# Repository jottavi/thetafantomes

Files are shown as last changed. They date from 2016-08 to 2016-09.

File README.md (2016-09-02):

# Documentation Thêta Fantômes

---
## L'installation

### Mise en place

 1. Brancher le routeur wifi.
 2. Attendre que le voyant wifi soit allumé.
 3. Brancher les batteries sur les circuits jaune des plateformes (PAS SUR LA BLEUE, RISQUE DE DESTRUCTION).
 4. La plateforme devrait faire un bruit strident, elle est en marche.
 5. Brancher le module de contrôle des lasers.

### Troubleshooting

*"La plateforme fait un bruit étrange et ne roule pas correctement, voir vibre."*

* La batterie est probablement vide, il faut la recharger ou en utiliser une autre pleine.

*"La plateforme ne roule pas correctement, les moteurs ne forcent pas ou forcent peu lors de la mise sous tension et ne font pas de bruit, voir vibrent."*

* Les drivers n'envoient peut-être pas assez de courant aux moteurs. Il faut donc tourner chaque potentiomètre des drivers avec UN TOURNE VIS CÉRAMIQUE jusqu'à ce qu'ils fassent un bruit et que les moteurs soient bloqués.

*"Un moteur ne fonctionne pas du tout, n'est pas bloqué, et même en tournant le potentiomètre du driver cela n'a aucun effet."*

* Le driver est probablement grillé. Il faut tester avec un nouveau driver.

*"La plateforme est sous tension, fait du bruit mais n'avance pas lorsque l'ordinateur lui envoie une information."*

* Vous avez surement branché les plateformes trop tôt après avoir branché le routeur wifi, attendez que le voyant WIFI de celui-ci s'allume pour débranchez et rebranchez la plateforme.

*"Le module de contrôle des lasers est sous tension mais les lasers ne bougent pas lorsque l'ordinateur lui envoie une information."*

* Vous avez surement branché le module trop tôt après avoir branché le routeur wifi, attendez que le voyant WIFI de celui-ci s'allume pour débrancher et rebrancher le module de contrôle des lasers.

## Technique

À [cette adresse](https///github.com/jottavi/thetafantomes), vous trouverez le dossier contenant :

* le code
* les librairies
* les pièces 3D
* les circuits imprimés
* les drivers

### Wifi

#### Network

Voici les IP et les ports sur lesquels les dispositifs fonctionnent :

<table>
	<thead>
		<tr>
			<th>Dispositifs</th>
			<th>IP</th>
			<th>PORT</th>
			<th>Envoi / Réception</th>
		</tr>
	</thead>
	<tbody>
		<tr>
			<td>Master Machine</td>
			<td>192.168.168.100</td>
			<td>7110</td>
			<td>Envoi &gt; Broadcast</td>
		</tr>
		<tr>
			<td>Laptop Player 1</td>
			<td>192.168.168.101</td>
			<td>7110</td>
			<td>Envoi &gt; Broadcast</td>
		</tr>
		<tr>
			<td>Laptop Player 2</td>
			<td>192.168.168.102</td>
			<td>7110</td>
			<td>Envoi &gt; Broadcast</td>
		</tr>
		<tr>
			<td>Laptop Player 3</td>
			<td>192.168.168.103</td>
			<td>7110</td>
			<td>Envoi &gt; Broadcast</td>
		</tr>
		<tr>
			<td>Laptop Player 4</td>
			<td>192.168.168.104</td>
			<td>7110</td>
			<td>Envoi &gt; Broadcast</td>
		</tr>
		<tr>
			<td>Lasers</td>
			<td>192.168.168.200</td>
			<td>7110</td>
			<td>Réception &gt; 192.168.168.101-102-103-104</td>
		</tr>
		<tr>
			<td>Plateforme Player 1 (Alpha)</td>
			<td>192.168.168.201</td>
			<td>7110</td>
			<td>Réception &gt; 192.168.168.101</td>
		</tr>
		<tr>
			<td>Plateforme Player 2 (Bravo)</td>
			<td>192.168.168.202</td>
			<td>7110</td>
			<td>Réception &gt; 192.168.168.102</td>
		</tr>
		<tr>
			<td>Plateforme Player 3 (Charlie)</td>
			<td>192.168.168.203</td>
			<td>7110</td>
			<td>Réception &gt; 192.168.168.103</td>
		</tr>
		<tr>
			<td>Plateforme Player 4 (Tango)</td>
			<td>192.168.168.204</td>
			<td>7110</td>
			<td>Réception &gt; 192.168.168.104</td>
		</tr>
	</tbody>
</table>

Le module de contrôle des lasers écoute sur toutes les IPs des ordinateurs des joueurs et actionne le laser correspondant au joueur attribué.

Les messages OSC peuvent être envoyés jusqu'à 10 millisecondes sur les lasers, pas moins. Peut-être plus pour les plateformes.

Voici les messages OSC réceptionnés par les dispositifs (plateformes et lasers) :

<table>
	<thead>
		<tr>
			<th colspan="3">Plateformes</th>
		</tr>
		<tr>
			<th>Route</th>
			<th>Valeurs</th>
			<th>Effet</th>
		</tr>
	</thead>
	<tbody>
		<tr>
			<td>/speed</td>
			<td>-10000 => 10000</td>
			<td>Vitesse</td>
		</tr>
		<tr>
			<td>/angle</td>
			<td>-180 => 180</td>
			<td>Rotation</td>
		</tr>
	</tbody>
	</tr>
</table>

<table>
	<thead>
		<tr>
			<th colspan="3">Lasers</th>
		</tr>
		<tr>
			<th>Route</th>
			<th>Valeurs</th>
			<th>Effet</th>
		</tr>
	</thead>
	<tbody>
		<tr>
			<td>/x</td>
			<td>0 => 127</td>
			<td>Position X</td>
		</tr>
		<tr>
			<td>/y</td>
			<td>0 => 127</td>
			<td>Position Y</td>
		</tr>
		<tr>
			<td>/blink</td>
			<td>0 => 171 (0 = OFF / 171 = ON)</td>
			<td>Clignotement</td>
		</tr>
	</tbody>
	</tr>
</table>

#### Programmation

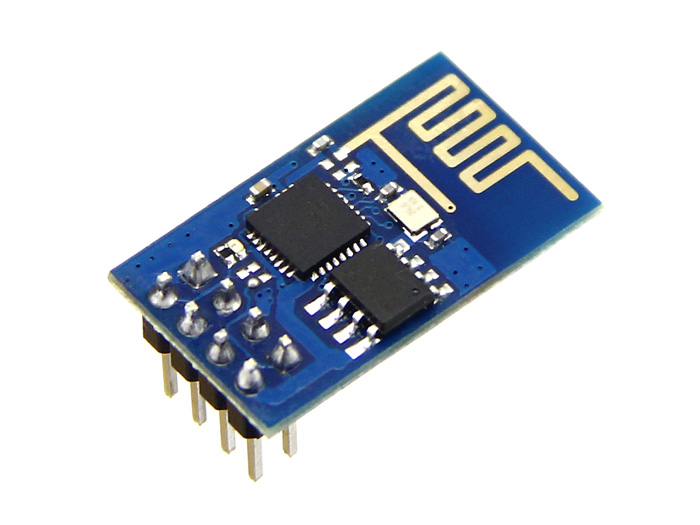
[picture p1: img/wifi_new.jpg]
ESP8266


Le module wifi utilisé (ESP8266) contient un petit microcontrôleur programmable et une puce wifi.  
Aussi, pour une meilleur gestion des messages OSC, le module a dû être reprogrammé à partir de l'IDE arduino, en y installant une librairie de gestion du protocole OSC.  
Vous trouverez la documentation de cette librairie à [cet endroit](https///github.com/CNMAT/OSC), et le reste des fonctions se trouvent [ici](http://cnmat.berkeley.edu/library/oscuino/).  
La version utilisée est adaptée pour l'ESP8266, vous la trouverez dans le dossier du projet et à [cette adresse](https///github.com/sandeepmistry/esp8266-OSC).  
Vous pouvez toujours remettre le firmware d'origine, disponible sur le site d'espressif.

Le module MOD-WIFI-ESP8266 de chez Olimex est un mauvais choix de version de module, nécessitant une soudure pour pouvoir le reprogrammer (voir image ci-dessous). En revanche, d'autres modules sont excellents, comme le NodeMcu Lua ESP8266, utilisable plus facilement en standalone, sans arduino, mais sur lequel il est difficile d'ajouter un shield.  

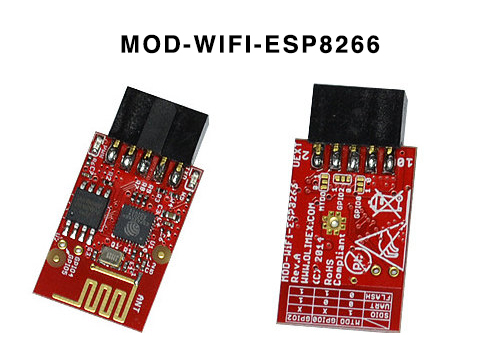
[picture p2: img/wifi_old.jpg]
MOD-WIFI-ESP8266


Il est nécessaire d'installer des outils pour pouvoir flasher ces modules avec un nouveau code.

##### Installation des outils de programmation dans l'IDE arduino

Pour commencer à programmer les ESP8266, vous aurez besoin d'installer les librairies relatives à ce module :

* Lancez arduino.
* Aller dans *Arduino > Préférences*.
* Sur cette fenêtre, entrez l'url *http://arduino.esp8266.com/stable/package\_esp8266com\_index.json* dans le champs *"URL de gestionnaire de cartes supplémentaires"* (Image ci-dessous).

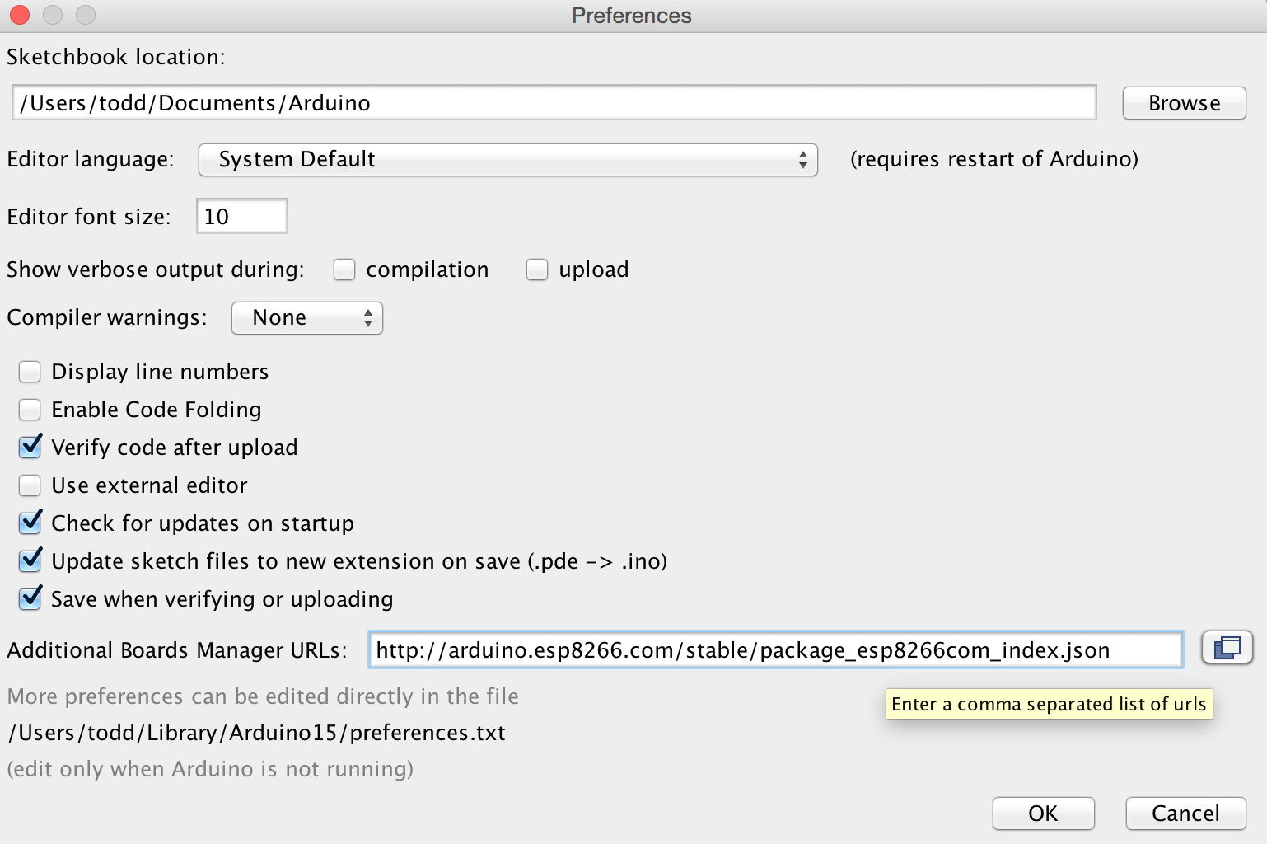
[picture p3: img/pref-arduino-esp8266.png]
Ajouter une URL de manager de cartes


* Cliquez sur OK.
* Allez dans *Outils > Type de carte > Gestionnaire de carte*.
* Dans cette fenêtre, recherchez *"esp8266"* et installez la librairie correspondante (voir ci-dessous).

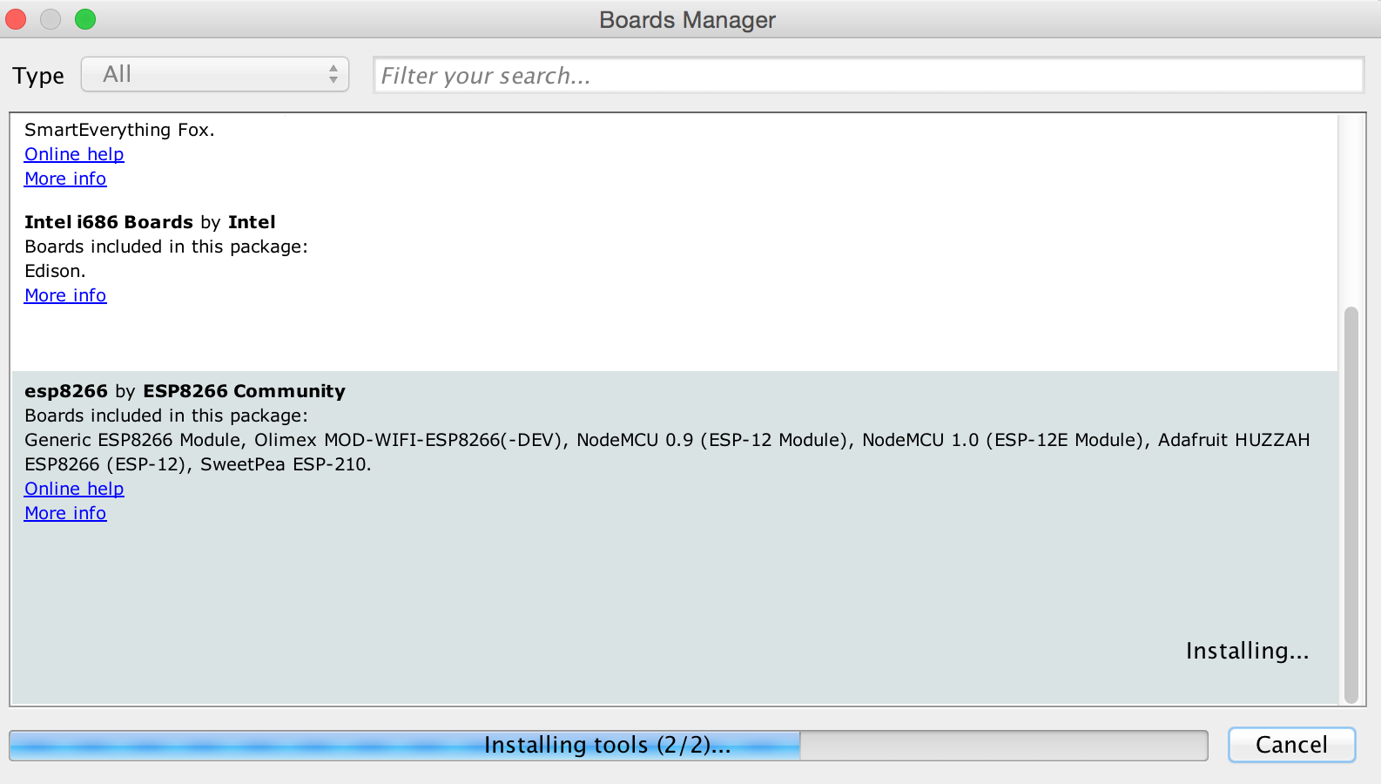
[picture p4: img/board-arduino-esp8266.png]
Installer le module ESP8266 sur l'IDE arduino


##### Installation du programmeur de l'ESP8266

Pour programmer ce module, nous allons avoir besoin de ce programmeur (voir image), plus simple à utiliser, basé sur la puce CH340.

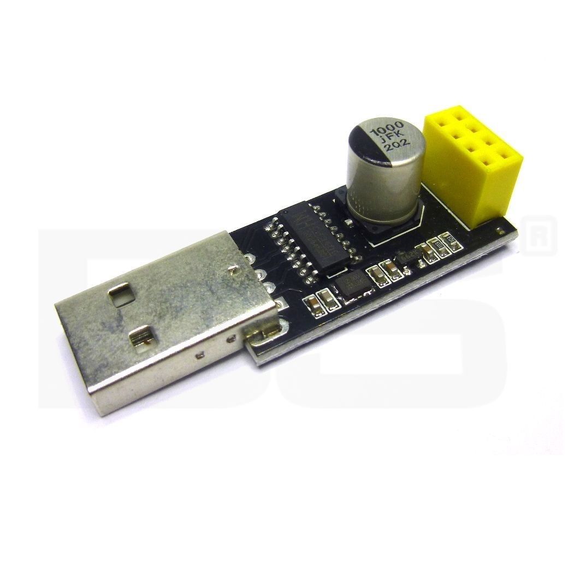
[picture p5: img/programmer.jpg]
Programmeur de l'ESP8266


Les drivers pour cette puce et les instructions d'installation sont présents à [cette page](http://sparks.gogo.co.nz/ch340.html).  
Vous les retrouverez dans le dossier du projet, disponible sur github. Sur linux, il n'est peut-être pas nécessaire de les installer.

##### Uploader un sketch sur l'ESP8266

Une fois ces étapes réalisées, vous devez sélectionner certains paramètres afin de programmer le module.

* Dans Arduino, allez dans *Outils > Type de Carte* et choisissez *"Generic ESP8266 Module"*.

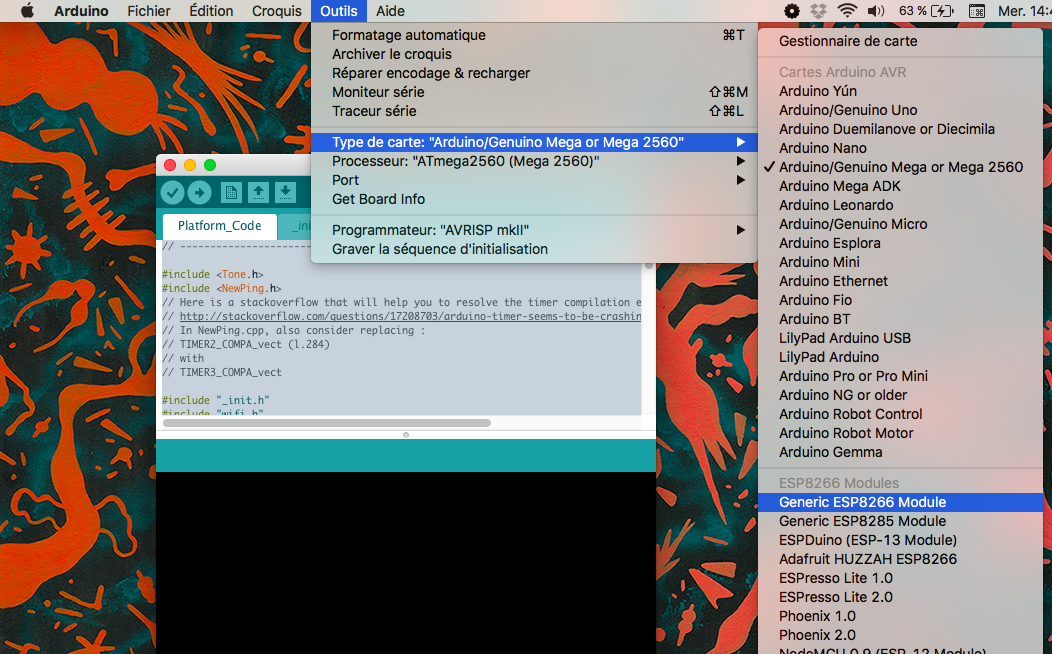
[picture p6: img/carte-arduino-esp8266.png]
Carte à selectionner


* Ensuite, lorsque le programmeur est branché, allez dans *Outils > Port* et choisissez *"/dev/cu.wchusbserial410"*.

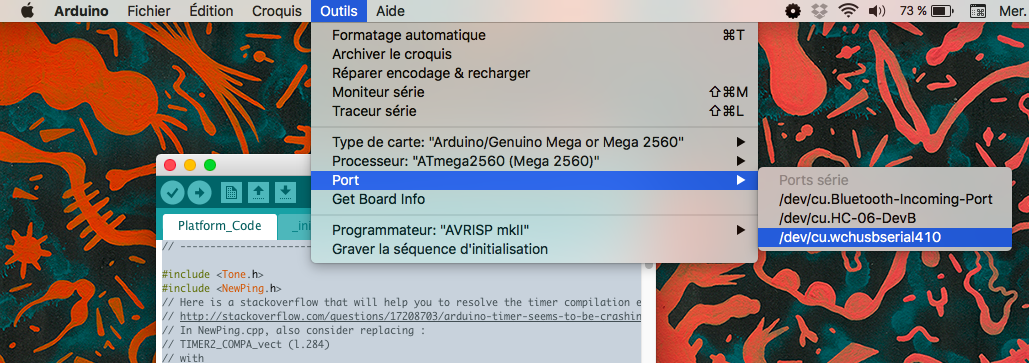
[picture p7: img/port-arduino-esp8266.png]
Port à selectionner


* Vous pouvez uploader le code.

### Lasers

Le code des lasers est très simple et met en oeuvre une Arduino Uno, un module wifi ESP8266 et un Tinkerkit Dmx Master Shield.  
Comme pour les plateformes, le module wifi relaie l'information osc vers l'arduino uno qui pilote les lasers via le shield DMX.

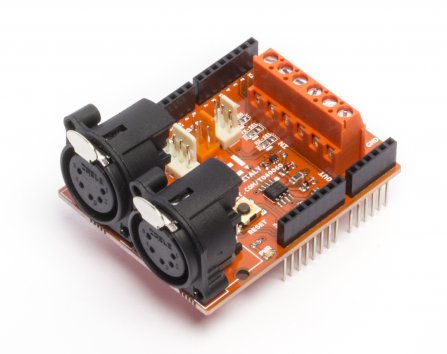
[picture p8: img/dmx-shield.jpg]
Tinkerkit DMX Master Shield


En revanche, le shield DMX comprend des embases XLR femelles 5 broches non compatibles avec les câbles XLR 3 broches couramment utilisés.  
Voici un schéma de montage pour construire un adaptateur XLR 5 broches vers XLR 3 broches afin de rendre ces câbles compatibles avec le shield.

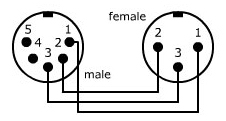
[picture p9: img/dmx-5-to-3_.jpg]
DMX 5 broches vers 3 broches


Le shield est pilotable par la librairie DmxSimple, disponible dans le dossier du projet et utilise la broche digital 3 de l'arduino UNO pour envoyer les commandes DMX.

Ces librairies se trouvent dans le dossier du projet. Vous trouverez la page de DmxSimple à [cette adresse](https///github.com/PaulStoffregen/DmxSimple).  
Pour installer une librairie arduino sur votre IDE, suivez [ce lien](https///www.arduino.cc/en/Guide/Libraries).

### Plateformes

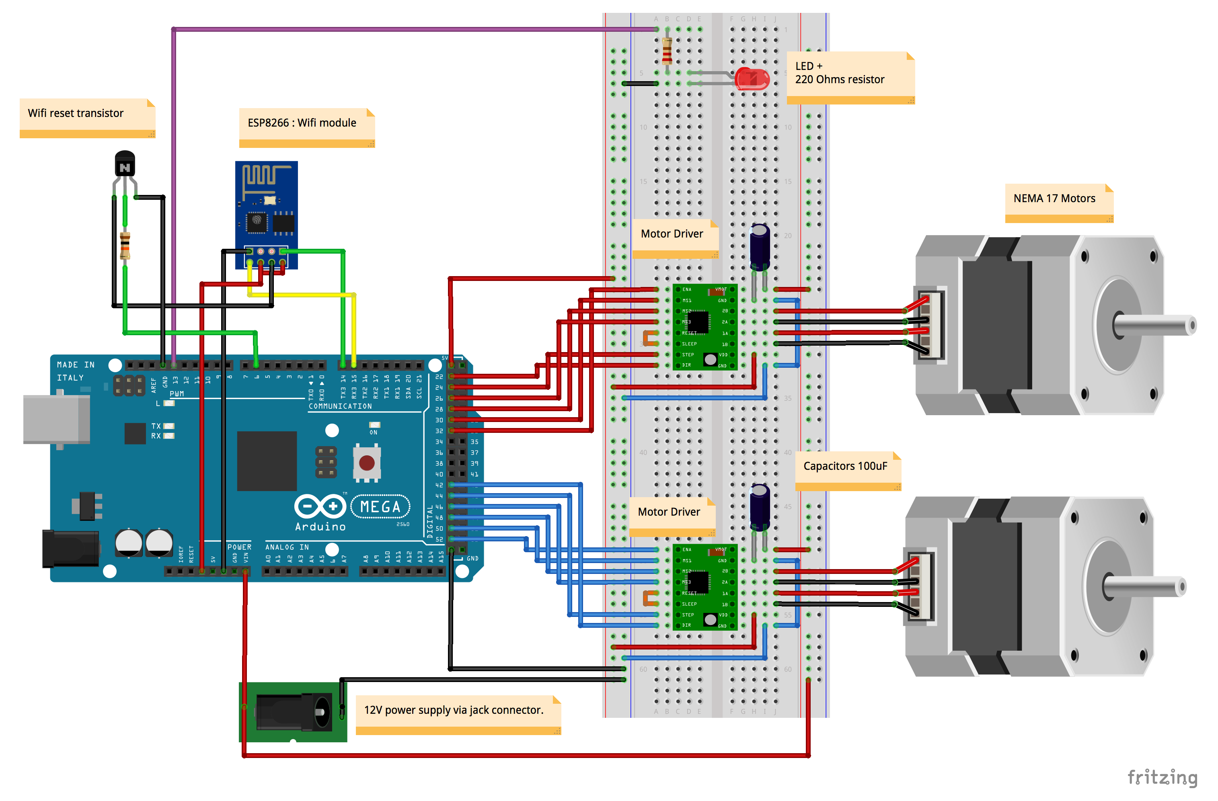
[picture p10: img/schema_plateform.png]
Schéma de l'électronique des plateformes


Schéma réalisé avec Fritzing.

#### Uploader le bon player

__*Dans le fichier \_init.h du code des plateformes, vous trouverez dans les premières lignes une macro appelée "PLAYER_ID".  
En changeant cette ID par 1, 2, 3 ou 4, on change aussi le player contrôlant la plateforme.*__

Chaque module Wifi correspond à une plateforme, dans le sens ou leur adresse MAC est fixée sur le routeur.

#### Moteurs & Drivers

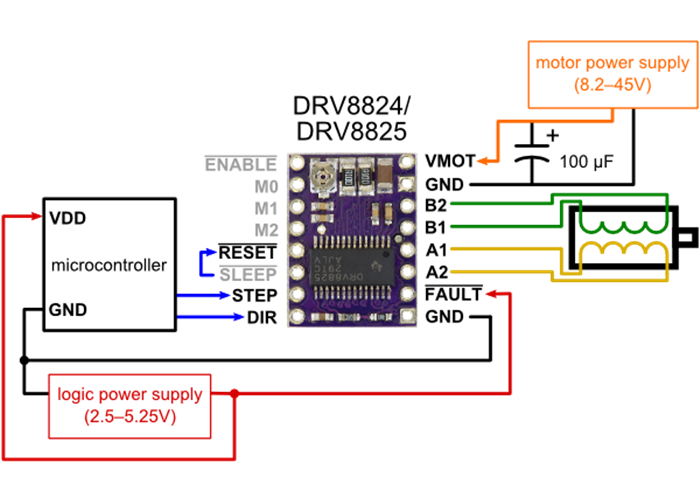
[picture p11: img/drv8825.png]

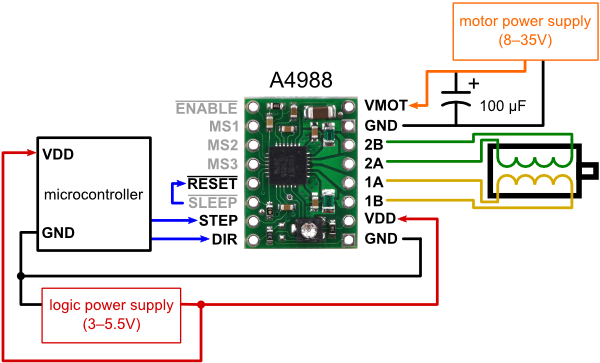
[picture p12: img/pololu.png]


Les branchements du schéma ont été trouvés à [cette adresse](http://wiki.mchobby.be/index.php?title=A4988).

On trouve différents types de circuits compatibles avec les shields des plateformes, triés ci-dessous par efficacité :

 1. [COOLDRV8825](https///www.reprap-france.com/produit/407-pilote-de-moteur-pas-a-pas-cooldrv8825) => Le meilleur, extrêmement puissant
 2. DRV8825
 3. Pololu A4988 Black Edition
 4. Pololu A4988
 5. copies chinoises, à éviter, fonctionnent très mal

__*/!\ ATTENTION, LES DRV8825 SE BRANCHE DANS LE SENS INVERSE DES POLOLU A4988, voir images ci-dessous/!\ *__

Une fois la plateforme sous tension, on doit tourner le potentiomètre sur le pololu pour augmenter l'ampérage de sortie et donc la puissance des moteurs. Il faut essayer de bouger la plateforme pour vérifier le niveau d'ampérage utilisé.  
Cette manipulation doit s'effectuer avec un tourne vis en céramique pour ne pas abîmer les drivers (un tourne-vis en métal conduit le courant).

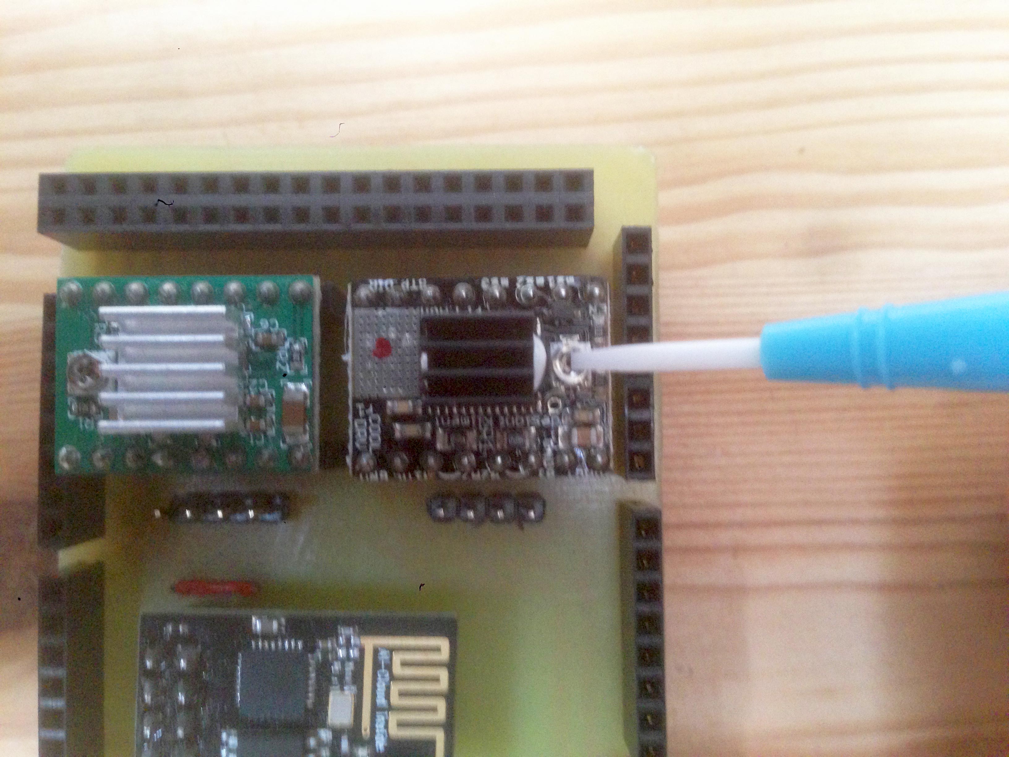
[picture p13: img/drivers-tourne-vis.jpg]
Potentiomêtre de réglage des drivers

Tourne-vis céramique

Les moteurs sont contrôlés par les drivers sur 6 ports digitaux :

* ENABLE : Active le pololu et le bloquage du moteur lorsque la broche est en LOW (logique inversée).
* STEP : En passant cette branche sur HIGH puis sur LOW (avec un delai), le moteur fait un pas.
* DIR : Sélectionne le sens de rotation du moteur (ex: LOW -> avance, HIGH -> recule).
* MS1, MS2, MS3 : Définissent la précision du pas (1/4, 1/8, 1/16, voir 1/32 pour les DRV8825).

Nous avons choisi de mettre la précision sur 1/32 de pas (avec un DRV8825) pour que le moteur fasse moins de bruit et que le mouvement soit plus linéaire. Cette précision est modifiable en changeant les signaux entrants sur les ports MS1, MS2 et MS3 des drivers comme ceci (pour un DRV8825) :

 | MS1  | MS2  | MS3  | Resolution du Micro-pas          | 
 | ---  | ---  | ---  | -----------------------          | 
 | LOW  | LOW  | LOW  | Pas de microstepping (full step) | 
 | HIGH | LOW  | LOW  | Demi-pas (half step)             | 
 | LOW  | HIGH | LOW  | 1/4 pas                          | 
 | HIGH | HIGH | LOW  | 1/8 pas                          | 
 | LOW  | LOW  | HIGH | 1/16 pas                         | 
 | HIGH | LOW  | HIGH | 1/32 pas                         | 
 | LOW  | HIGH | HIGH | 1/32 pas                         | 
 | HIGH | HIGH | HIGH | 1/32 pas                         | 

À chaque fois que le signal sur la broche STEP du drivers effectue une période HIGH/LOW, le moteur fait un pas.  
Ainsi, pour contrôler la vitesse des moteur, le code développé utilise une fonction permettant de générer une onde carrée à une fréquence donnée sur une broche de l’arduino, envoyée vers la broche STEP du driver, ce qui fait avancer le moteur plus vite si la fréquence est haute, et plus lentement si la fréquence est basse.

Cette librairie se trouvent dans le dossier du projet. Vous trouverez la page de la librairie à [cette adresse](https///code.google.com/archive/p/rogue-code/wikis/ToneLibraryDocumentation.wiki) et un exemple d’utilisation de cette librairie à [cette page](http://blog.ocad.ca/wordpress/digf6l01-fw201402-01/2014/10/using-arduino-to-play-two-tones-simultaneously/).  
Pour installer une librairie arduino sur votre IDE, suivez [ce lien](https///www.arduino.cc/en/Guide/Libraries).

#### Mécanique & construction

##### Installation de la sculpture sur les plateformes

ATTENTION, lors de l'installation d'une sculpture sur une plateforme, assurez-vous que la tige soit encastrée dans le deuxième socle (le petit sur la plaque de bois inférieure).  
Ne pas hésiter à forcer sur la barre pour la faire glisser dans le socle.

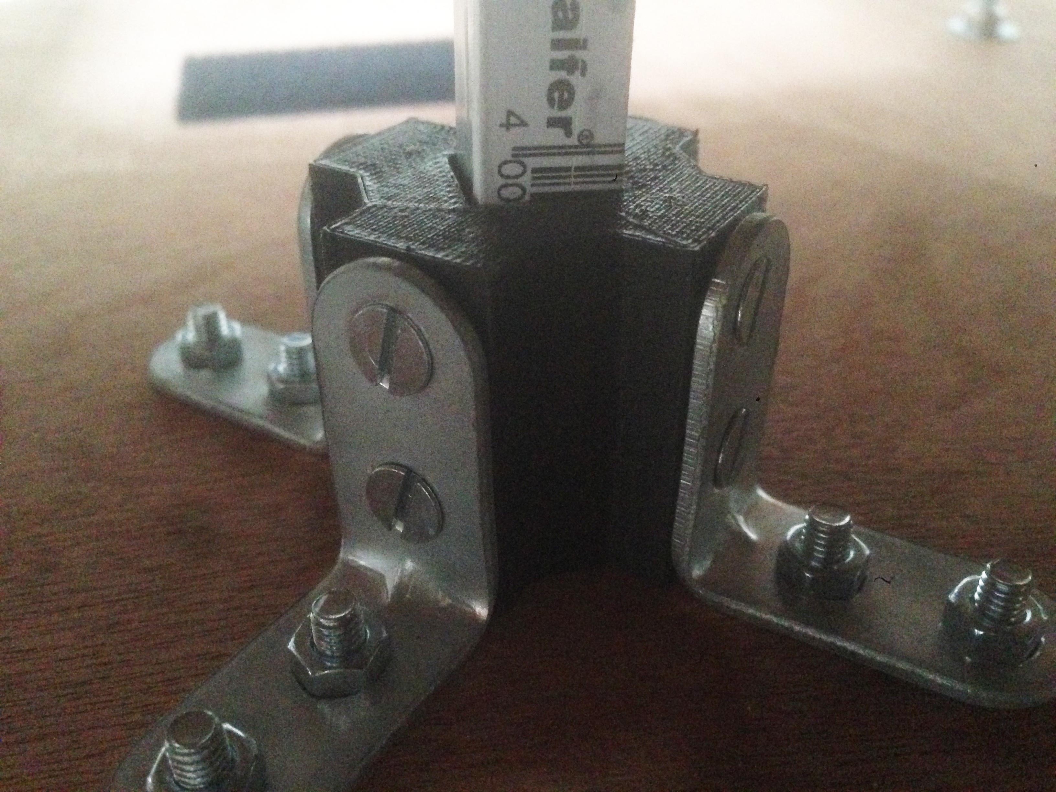
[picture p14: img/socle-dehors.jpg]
Barre en dehors du socle

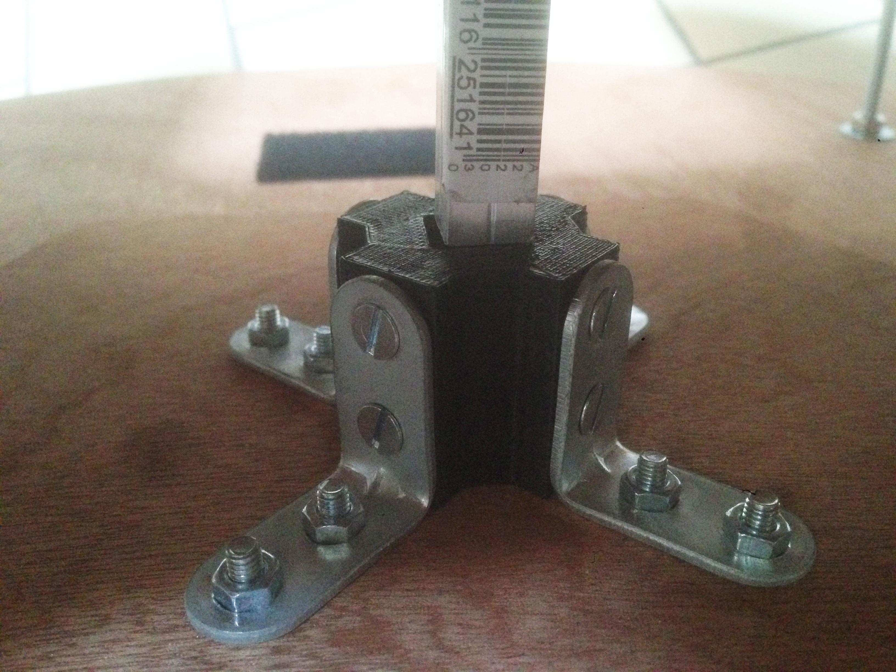
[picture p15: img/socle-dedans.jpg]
Barre dans le socle


Image du haut : en dehors / image du bas : dedans.

##### Modèles 3D

Si une pièce imprimée en 3D vient à être détruite, vous pouvez toujours en ré-imprimer une à partir des fichiers présents dans le dossier du projet, à l'aide de [ce tutoriel](tuto_imprimante_3d).

##### Améliorations possibles

* __Ventilateur__ : Pour mieux refroidir les drivers de moteur, il peut être bon d'ajouter un petit ventilateur au-dessus de ceux-ci. (Même si les COOLDRV8825 se refroidissent très bien.)
* __Batterie__ : Les changer pour des batteries du style [NiMh 12V environ 4000mAh](http://www.batteryspace.com/airsoftgunbattery12v4200mahnimhbatterypackforairsoftmodguns.aspx). Ce sont des batteries qui ont plus de cycles de recharge, qui sont plus rapides à charger, et (beaucoup) moins lourdes que les batteries au plomb.
* __Roues/stabilisateurs__ : Utiliser des [stabilisateurs (ball caster) avec des billes en nylons](https///www.pololu.com/product/2692), un matériau très silencieux lors de frictions avec une autre surface. En revanche, attention à la hauteur de ces stabilisateurs, peut-être trop hauts pour être fixés sur les plateformes.
* __Protection du bois__ : L'humidité et la lumière peuvent faire gondoler le bois. Un saturateur pour bois peut être appliqué sur celui-ci ou bien des plaques peuvent être redécoupées dans du contre-plaqué marin, très résistant à l'eau.

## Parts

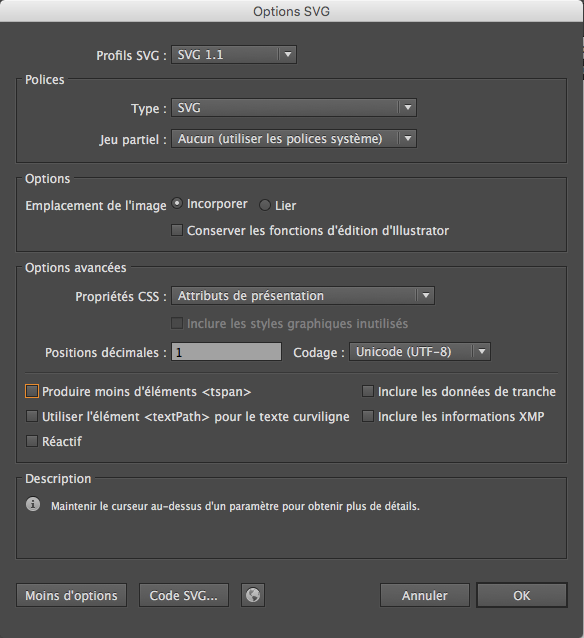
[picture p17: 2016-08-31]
circuits/shield_mega/external_parts/Pololu_A4988/illustrator_settings.png

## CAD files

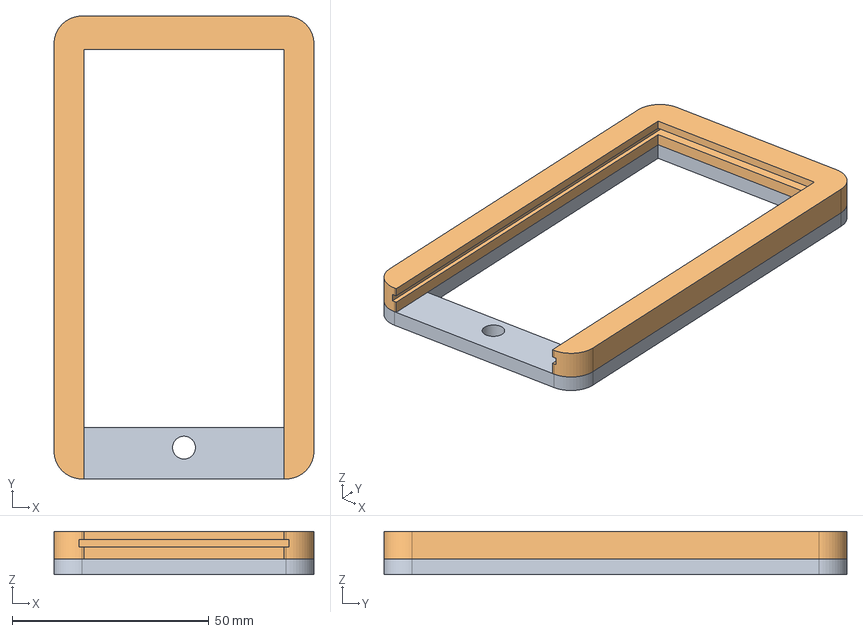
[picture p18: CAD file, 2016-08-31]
3d_parts/arduino_mount/arduino_mount.FCStd
66.0 x 117.5 x 11.0 mm

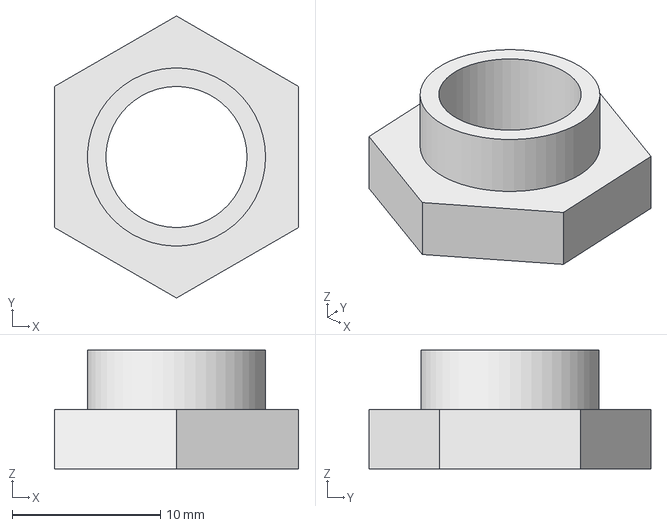
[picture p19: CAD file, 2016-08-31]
3d_parts/essieu/essieu.FCStd
16.5 x 19.0 x 8.00 mm

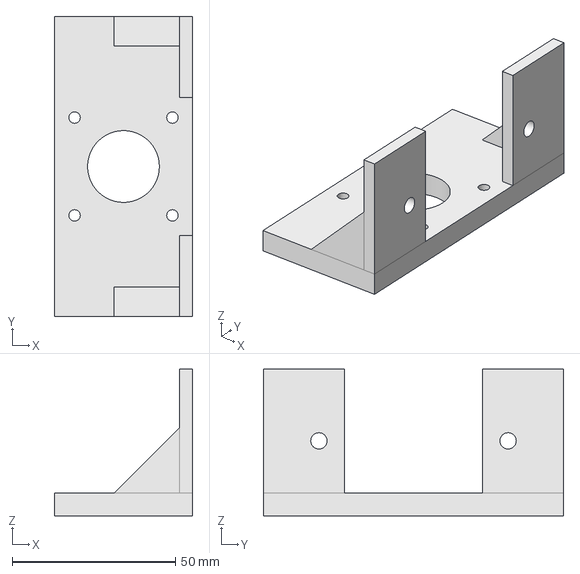
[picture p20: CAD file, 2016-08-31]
3d_parts/motor_mount/motor_mount.FCStd
42.3 x 92.0 x 45.0 mm

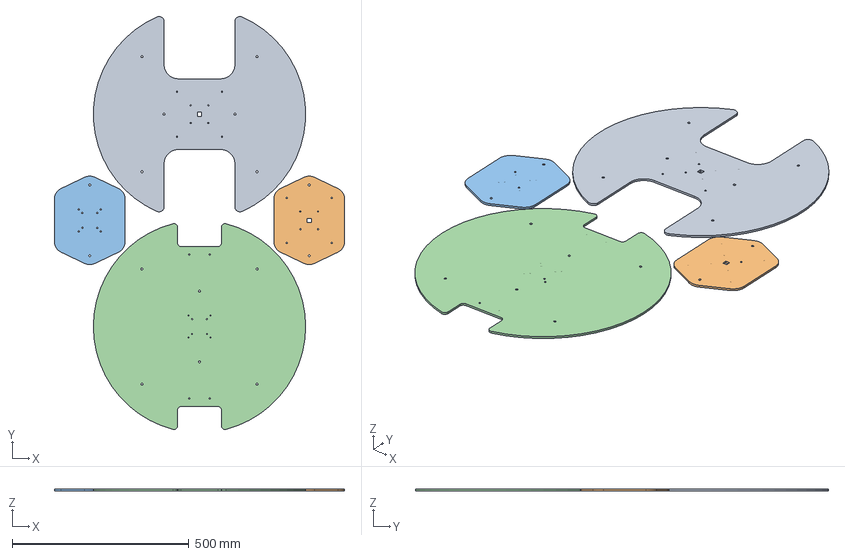
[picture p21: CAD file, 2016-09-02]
3d_parts/plaques/plaques.FCStd
820.0 x 1166.9 x 5.00 mm
top
socle_top
socle_bottom
bottom

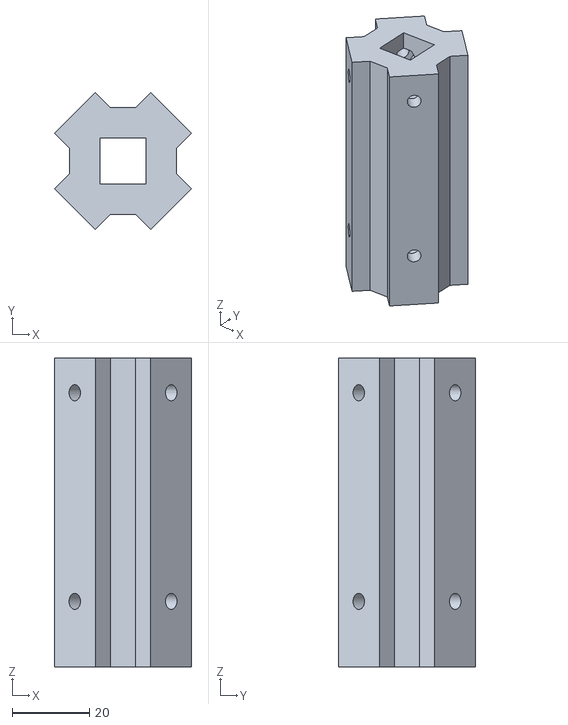
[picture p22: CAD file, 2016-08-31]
3d_parts/sculpture/grand_socle.stl
35.6 x 35.6 x 80.0

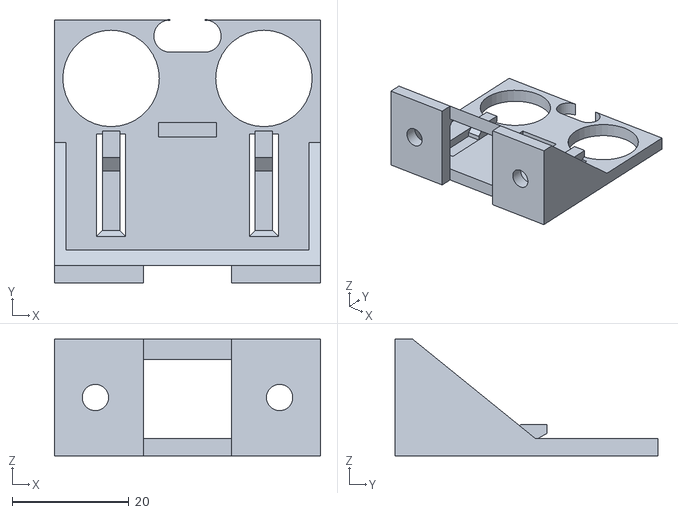
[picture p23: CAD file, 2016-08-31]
3d_parts/sensors/sensors.stl
45.5 x 45.0 x 20.0

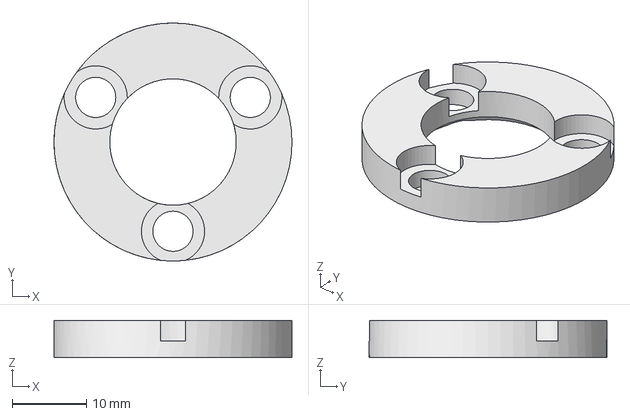
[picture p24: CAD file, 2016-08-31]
3d_parts/wheel/wheel.FCStd
32.0 x 32.0 x 5.00 mm

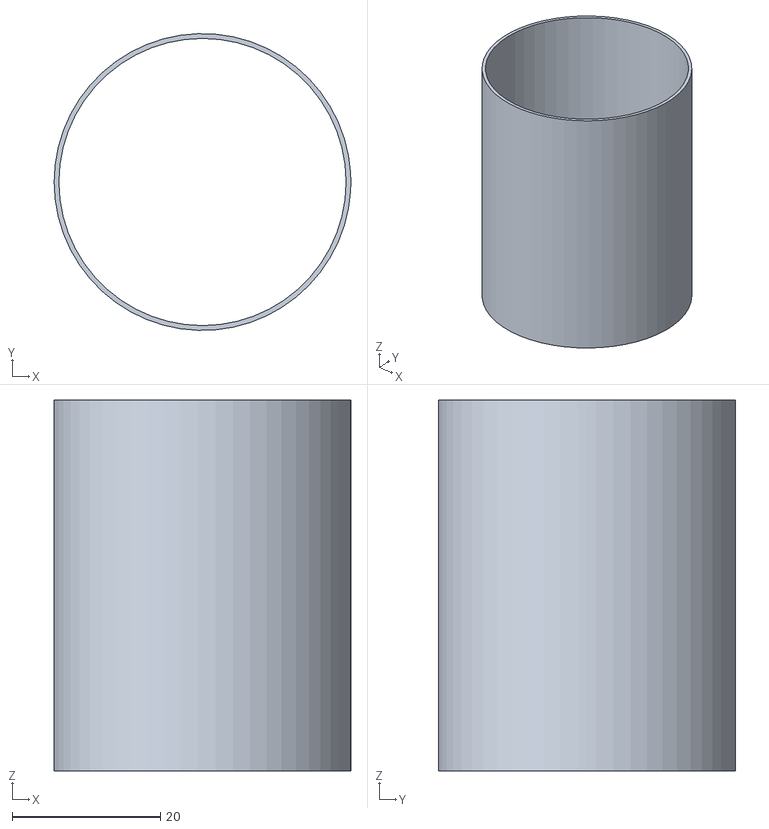
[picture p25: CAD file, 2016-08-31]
DELTA MICRO/calibre.STL
40.0 x 40.0 x 50.0

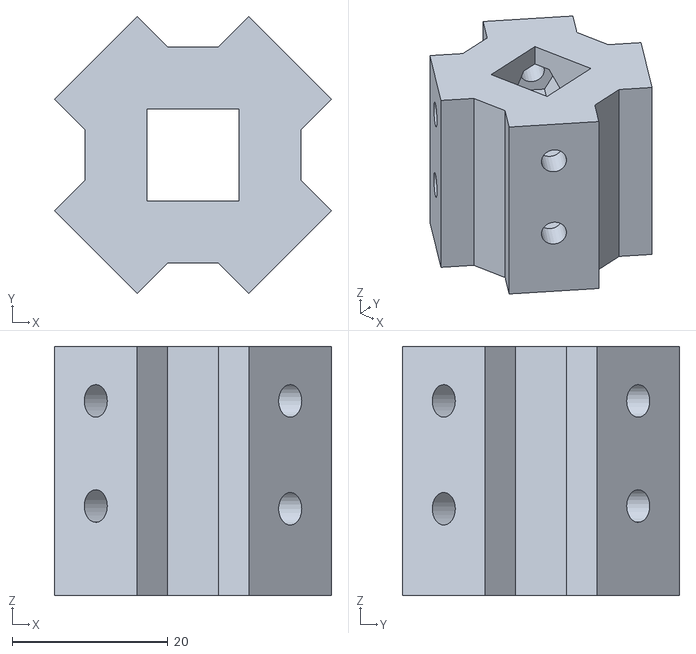
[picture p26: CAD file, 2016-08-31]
3d_parts/sculpture/petit_socle.stl
35.6 x 35.6 x 32.0

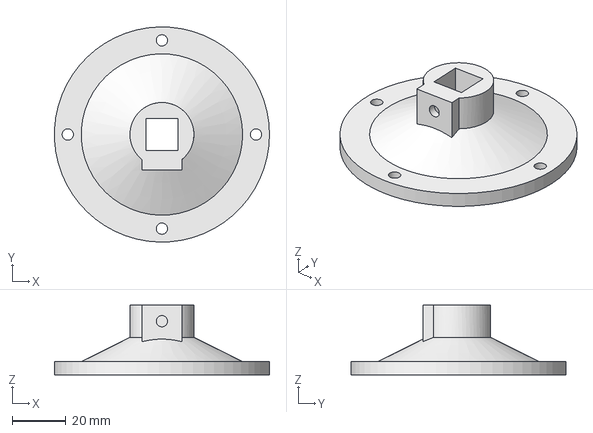
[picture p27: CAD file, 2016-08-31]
3d_parts/sculpture/mobile.FCStd
79.9 x 80.0 x 26.0 mm

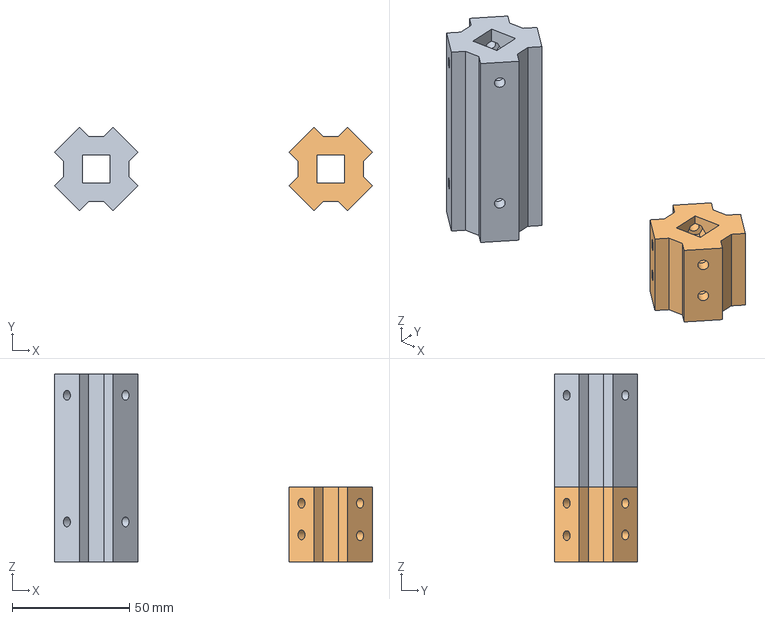
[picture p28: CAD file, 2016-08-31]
3d_parts/sculpture/socles.FCStd
135.6 x 35.6 x 80.0 mm
grand_socle
petit_socle

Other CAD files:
3d_parts/arduino_mount/arduino_mount.stl
3d_parts/essieu/essieu.stl
3d_parts/motor_mount/motor_mount.stl
3d_parts/plaques/plaques.stl
3d_parts/sculpture/mobile.stl
3d_parts/wheel/wheel.stl

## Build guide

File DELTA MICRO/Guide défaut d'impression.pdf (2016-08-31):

# RepRap printDoctor

Cet article veut être une aide au diagnostic et à la correction des défauts d’impression : il tente de répertorier une certain nombre de petits problèmes que nous pouvons rencontrer lors de l'impression 3D de pièces avec nos imprimantes de type RepRap. Il s'agit de :
- identifier les défauts d'impression,
- en analyser les causes
- y proposer des remèdes.
Ce travail est initié par Philippe, Pierrot et Franck (de Gi-Nova) : nous espérons que chaque possesseur d'imprimante 3D pourra non seulement y puiser quelques idées, mais aussi corriger certaines analyses que nous avons faites, ou compléter l'article en recensant des défauts non encore listés (car nous sommes persuadés de ne pas avoir fait le tour des problèmes ;-) ) L'objectif est donc d'en faire une ressource participative : n'hésitez pas à participer !
Références externes :
- support.3dverkstan.se (http://support.3dverkstan.se/article/23-a-visual-ultimaker-troubleshooting-guide) Pour les ultimaker mais utile quand même. (Anglais)
- wiki reprap.org (http://reprap.org/wiki/Print_Troubleshooting_Pictorial_Guide) Guide visuel (photos) pour diagnostiquer la source de vos problèmes (Anglais)

## Défaut n°1, ça bave

défaut numéro 1

Symptôme
De fins filaments sont tissés dans le vide entre différentes parties de la pièce. Keyword : oozing

Cause possible
Du plastique continue de s'écouler de la tête lors des déplacements de celle-ci, en raison de la pression résiduelle dans le corps de chauffe et de la fluidité du plastique fondu.

Correctifs proposés
- Augmenter la longueur de retrait du filament (retraction length dans Slic3r, retraction distance dans CuraEngine). Le recul du filament fait chuter la pression dans le corps de chauffe. L’effet peut être modulé en jouant aussi sur la vitesse de retrait.
- Augmenter la vitesse de déplacement de la tête. Cela laisse moins de temps au plastique fondu pour s’écouler.
- Diminuer la température d’extrusion. Celle-ci est peut-être trop élevée conduisant à un plastique plus fluide s’échappant plus rapidement par l’orifice de la tête.

## Défaut n°2, effondrement

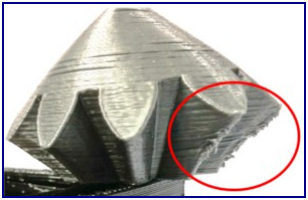
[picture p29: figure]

Surplomb

Symptôme
Effondrement ou mauvaise qualité d'une surface en surplomb. Keyword : overhang

Cause possible
La solidification du plastique déposé en périphérie du surplomb n’est pas assez rapide et le filament déposé bouge avant solidification. Le phénomène se répète ou s’accentue d’une couche à l’autre.

Correctifs proposés
- Ventiler plus efficacement le plastique déposé (localisation du flux d’air, débit)
- Créer des supports
- Changer l'orientation de la pièce

## Défaut n°3, délaminage latéral sur périmètre ou face horizontale

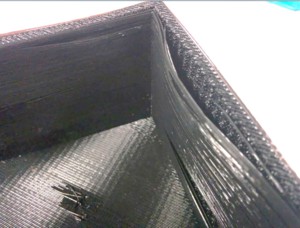
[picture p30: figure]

Délaminage, exemple 1

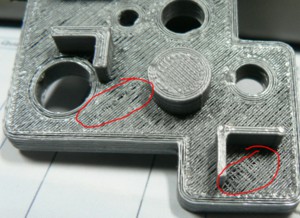
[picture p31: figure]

Délaminage, exemple 2

Symptômes
- Les périmètres sont insuffisamment liés entre eux, provoquant un délaminage de parois verticales.
- Les faces planes ne sont pas couvertes

Cause possible
- Pas suffisamment de matière déposée. Trop étroit, le cordon déposé ne touche pas suffisamment, et donc ne colle pas au cordon voisin.
- Présence d’impureté dans la buse qui gêne le passage de la matière fondue.
- La température d'extrusion est trop faible entrainant un défaut de collage au cordon voisin.

Correctifs proposés
- Calibrer l'extrudeur pour avoir un débit de matière conforme aux données du slicer.
- Déboucher la buse (foret, fil d’acier, extraction à 70°C,…)
- Augmenter la température d’extrusion
- Augmenter le taux de chevauchement (CURA)

## Défaut n°4, manque de matière dans une section mince

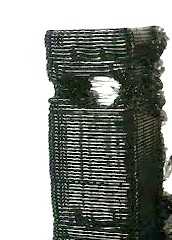
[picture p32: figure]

Symptôme
Section fine très mal remplie au niveau du trou dans la colonne (voir image)

Cause possible
- « back-retract » ou reprise après retract peu efficace
- Mauvaise solidification du fil
- Glissement de l'entraînement du filament lors des retracts

Correctifs proposés
- Diminuer la vitesse et la longueur de retraction
- Augmenter “extra legth on retract” (Slic3r)
- Augmenter la pression des ressorts sur l'idler

## Défaut n°5, boursoufflures

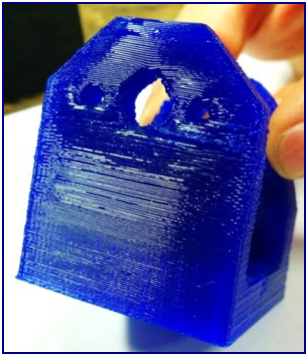
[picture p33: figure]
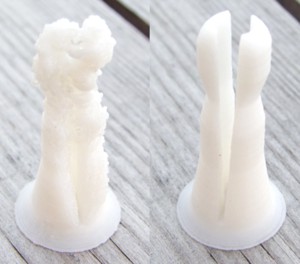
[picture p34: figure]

Symptôme
Boursouflures, géométrie non conforme, en particulier dans les sections de faible surface.

Cause possible
Filament trop chaud ou refroidissement inefficace

Correctifs proposés
- Mettre plus de pièces sur le plateau (l’impression d’une couche est alors plus longue, laissant au filament déposé le temps de refroidir et se solidifier avant le dépôt de la couche suivante).
- Mieux refroidir (orientation, débit, durée…)

## Défaut n°6, délaminage des parois minces

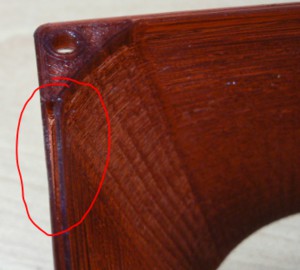
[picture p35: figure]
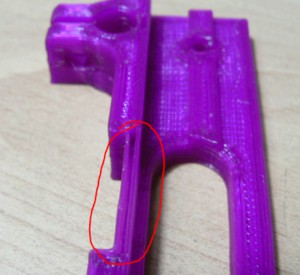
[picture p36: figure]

Symptôme
Une paroi mince, sans remplissage, voit ses fils se séparer, non collés entre eux latéralement.

Cause possible
Parois trop fines et d'épaisseur incompatible avec la largeur de filament.

Correctifs proposés
- Dessiner des épaisseurs de parois correspondant à un multiple de la largeur de filament

déposé.
- Imposer dans le paramétrage du slicer une largeur de dépôt sous-multiple de la largeur de paroi, tout en restant compatible avec le diamètre d’extrusion et la hauteur de couche.
- Changer de slicer: on a pu constater que dans ce type de situation Cura gère mieux le remplissage des parois que Slic3r (qui a par ailleurs d'autres avantages).

## Défaut n°7, décalage horizontal d'une couche

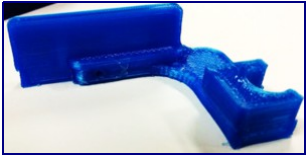
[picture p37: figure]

Symptôme
Décalage d'une couche suivant x ou y.

Cause possible
Défaut de déplacement de la tête ou du plateau.

Correctifs proposés
- Diminuer l'accélération sur l'axe concerné.
- Régler le courant dans le driver pololu.
- Mieux refroidir le driver pololu

## Défaut n°8, décalage régulier

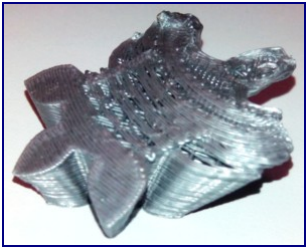
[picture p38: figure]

Symptôme
Décalage quasi systématique des couches suivant x ou y à partir d’une certaine hauteur d’impression.

Cause possible
Défaut de déplacement de la tête ou du plateau dû à une surchauffe des pololu qui se mettent en sécurité.

Correctifs proposés
- Refroidir les pololu (ventilation)
- Régler le courant dans le pololu

## Défaut n°9, cintrage vers le haut

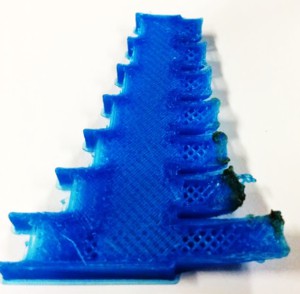
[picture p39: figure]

Keyword : curling

Symptôme
Déformation dans la direction z lors de l’impression, en particulier des zones à fort surplomb.

Cause possible
Mauvaise solidification, effet bilame (rétractation) dû à la différence de température du fil déposé sur la couche précédente déjà plus froide.

Correctifs proposés
- Augmenter la pente au niveau du dessin de la pièce, de manière à atténuer le surplomb
- Refroidir davantage le plastique déposé
- Mettre des supports

## Défaut n°10, décollement des angles

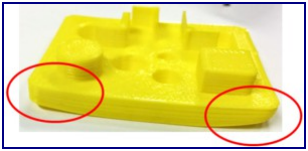
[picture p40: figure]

Symptôme
Les coins de la pièce se décollent du plateau et la base de la pièce n’est pas plane. Keyword : warping

Cause possible
- Mauvaise adhérence de la pièce au plateau
- Coefficient de retrait du matériau trop important
- Première couche pas assez « écrasée »

Correctifs proposés
- Changer de matériau
- Mettre de l'adhésif (colle, 3Dlaque, ruban adhésif…)
- Régler correctement la hauteur du plateau
- Imposer une première couche plus fine pour écraser davantage le cordon
- Construire un brim
- Chauffer le plateau
- Nettoyer, dégraisser le support
- Changer la stratégie de remplissage. Un remplissage de la face inférieure concentrique plutôt que linéaire permet d’avoir retrait plus isotrope, puis un remplissage de l’intérieur en nid d’abeille évite l’effet bilame.
- Diminuer la densité de remplissage intérieur

## Défaut n°11, densité extrusion faible

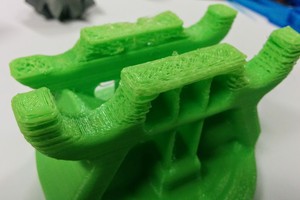
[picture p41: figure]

Symptôme
Densité de matière non conforme.

Cause possible
Flux de matière trop faible

Correctifs proposés
- Déboucher la buse
- Fil bloqué en amont de l'extrudeur
- Revoir l'entraînement du fil (problème à la vis moletée ?)
- comprimer plus les ressorts de pression sur le galet

## Défaut n°12, angles mal formés

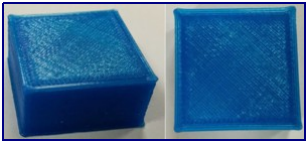
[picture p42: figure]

Symptôme
Angles pas assez vifs.

Cause possible
Surplus de matière dû à l'arrêt de la buse.

Correctifs proposés
- Adoucir volontairement l'angle de la pièce
- Augmenter le XYjerk

## Défaut n°13, gouttes noires

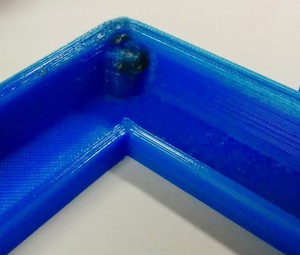
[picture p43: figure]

Symptôme
Présence de plastique brûlé (noirci)

Cause possible
Mauvaise étanchéité du nozzle, PLA brûlé qui s'écoule autour de la buse.

Correctifs proposés
Démonter le nozzle et refaire l'étanchéité !!

## Défaut n°14, couches mal soudées

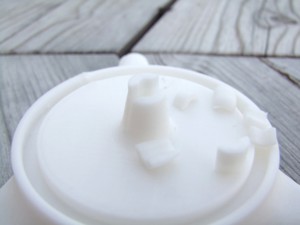
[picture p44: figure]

Symptôme
Pièce cassante au niveau de l’interface entre deux couches.

Cause possible
Refroidissement trop important, la couche déposée n’adhère pas bien à la couche précédente.

Correctifs proposés
- Diminuer la vitesse du ventilateur
- Augmenter la vitesse minimale d’impression (Repetier : Cooling thresholds -> min print speed)

## Défaut n°15, bulles

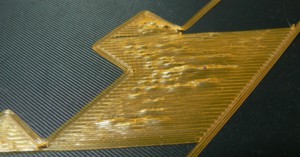
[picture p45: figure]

Symptôme
Première couche qui se décolle localement du plateau sous forme de bulles.

Causes possibles
- Présence dans le matériau d’humidité qui se vaporise progressivement au contact du plateau chauffant.
- Peut-être température insuffisante du heatbed pour ce type de PLA.

Correctifs proposés
- Stocker ses bobines de matériau brut au sec, sous emballage fermé, avec le sachet de déssicant.
- Sécher le matériau incriminé : passage au four à chaleur tournante à 40°C pendant 3h environ. Attention à ne pas chauffer au-delà de 45 ou 50°C: risque d’adhérence des fils les uns sur les autres dans la bobine, ou de perte de la cylindricité du fil.
- augmenter la température du heatbed (sur le cas de la photo, le problème a été résolu avec un heatbed à 75°C).
- imprimer sur du scotch

## Défaut n°16, Dessus-dessous fragile

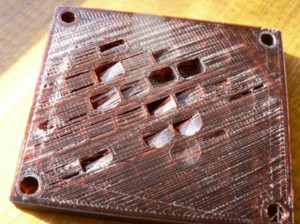
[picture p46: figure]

Symptôme
Faces horizontales trop fines et fragiles.

Causes possibles
manque d'épaisseur de matière sur ou sous un remplissage peu dense. Les fils déposés ont trop peu de points d'appui et s'effondrent entre les nervures du remplissage.

Correctifs proposés
Mettre au moins 2 (voire 3 sur un remplissage peu dense) couches complètement remplies (paramètre "Solid layers" dans Slic3r) pour les faces "top" et "bottom".

## Défaut n°17, Haut de trou

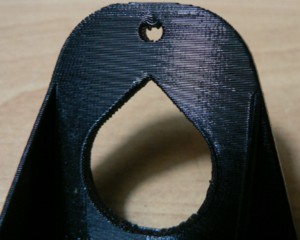
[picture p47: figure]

Symptôme
Les fils du haut d'un trou d'axe horizontal s'effondrent à la construction.

Causes possibles
- zone presque horizontale trop importante car trou de gros diamètre.
- mauvaise cohérence entre température de buse, refroidissement du fil déposé, et vitesse.

Correctifs proposés
- réduire ou supprimer cette zone presque horizontale, en modifiant la géométrie. Exemple sur le gros trous de la photo, en forme de goutte d'eau plutôt que cylindrique.
- rendre cette zone réellement horizontale, afin qu'elle soit traitée comme un "bridge" (--> traversée à vitesse rapide, et refroidissement intensif).
- éviter de trop ralentir dans cette zone, même si le temps d'impression de la couche est faible : dans Slic3r, onglet "Filament Settings", "Cooling thresholds", "Slow down if layer print time is below", ou augmenter dans le même onglet le "Min print speed".

## Défaut n°18, Variations de couleur/transparence

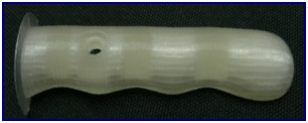
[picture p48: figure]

Symptôme
La couleur ou la transparence du matériau varie en fonction des sections.

Causes possibles
- différentes cristallisations du matériau dues à des vitesses de refroidissement différentes, liées au temps d'impression de chaque tranche (donc à la vitesse de dépose du fil), et à la puissance du ventilateur.
- idem, le dépôt d'une N'ième couche très chaude sur la couche N-1 insuffisamment refroidie qui voit sa température remonter. Le rayonnement de la buse peut aussi avoir un impact sur le cycle thermique de la couche précédente.
Noter que les propriétés physiques et mécaniques de la pièce peuvent varier en fonction de ces différences de cristallisation.

Correctifs proposés
- gérer le refroidissement via les paramètres du slicer :
- variation de puissance du ventilateur en fonction du temps de fabrication d'une tranche;
- ralentissement de la vitesse de dépose proportionnellement à la surface de la tranche.
- abaisser la température d'extrusion pour faciliter un changement de phase plus rapide et homogène.

## Défaut n°19, Délaminage entre couches

•

•

Symptôme
Certaines couches se cintrent et des fissures plus ou moins importantes apparaissent.

Causes possibles
- Le phénomène de "curling" dû à l'effet bilame (défaut n°9 ci-dessus) se produit entre les

couches.
- refroidissement du fil trop rapide en sortie de buse, il ne se soude pas correctement à la couche précédente.
- retrait (contraction) important du matériau au changement de phase et au refroidissement. Ce phénomène apparaît pour les matériaux extrudés à haute température (ABS, PC...) et présentant un retrait important.

Correctifs proposés
- modifier la température d'extrusion
- changer de matériau
- éviter de souffler sur le fil déposé ou réduire la puissance du ventilateur
- enfermer la zone de construction dans une enceinte régulée à une température proche de la transition vitreuse du matériau

## Défaut n°20, Votre machine fabrique des perles

Et pour le n°20 de cette liste de "défauts", un coup de chapeau à Pierrot qui a réussi cette magnifique perle des blagues de l'impression 3D :-))

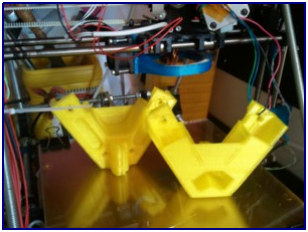
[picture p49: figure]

Symptôme
Un fil de votre imprimante passe dans un trou de la pièce imprimée. Ici sur la droite de la photo, un des 4 fils d'alimentation du moteur d'extrudeur semble-t-il.

Causes possibles
- des fils qui pendouillent là où ils ne devraient pas.
Ce phénomène apparaît souvent sur des machines tout juste en fin de montage, le constructeur, pressé d'imprimer ses premières pièces, n'ayant pas pris le temps d'un peu de rangement.

Correctifs proposés
- imprimer des pièces sans trous
- couper le fil pour récupérer la pièce
- casser la pièce pour récupérer le fil
- grouper proprement votre filasse avant d'imprimer la prochaine pièce
- ou alors planquer la photo au fond d'un tiroir en espérant qu'elle ne reviendra pas à la surface !

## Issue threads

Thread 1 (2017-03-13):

Perte connection wifi

papicambia, 2017-03-13:
La connection wifi entre la plateforme et l'ordinateur est perdue.
-> Vérifier les adressages ip dans le routeur wifi.
-> Charger le code aléatoire de secours

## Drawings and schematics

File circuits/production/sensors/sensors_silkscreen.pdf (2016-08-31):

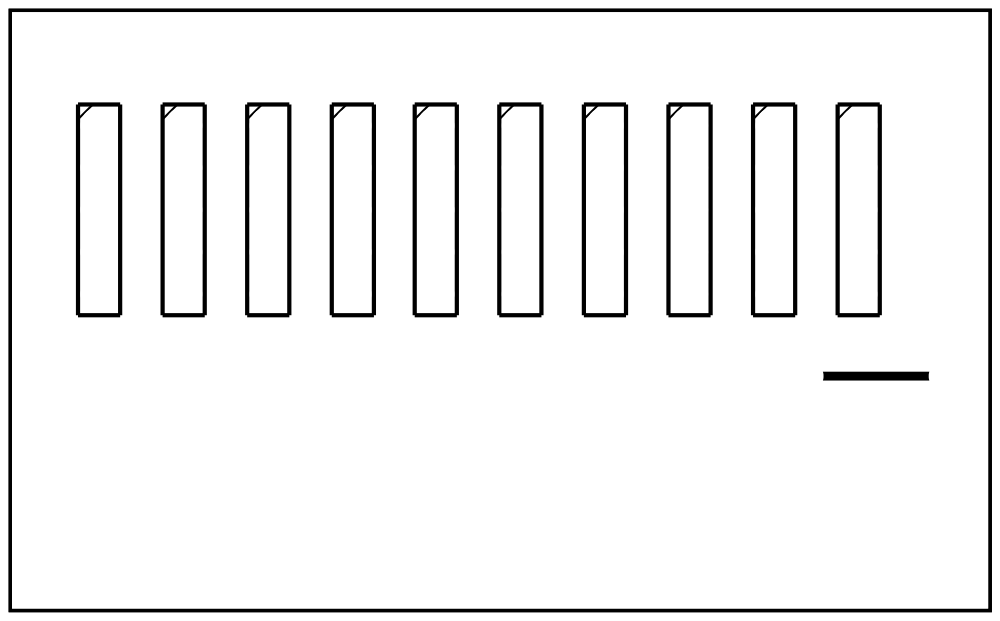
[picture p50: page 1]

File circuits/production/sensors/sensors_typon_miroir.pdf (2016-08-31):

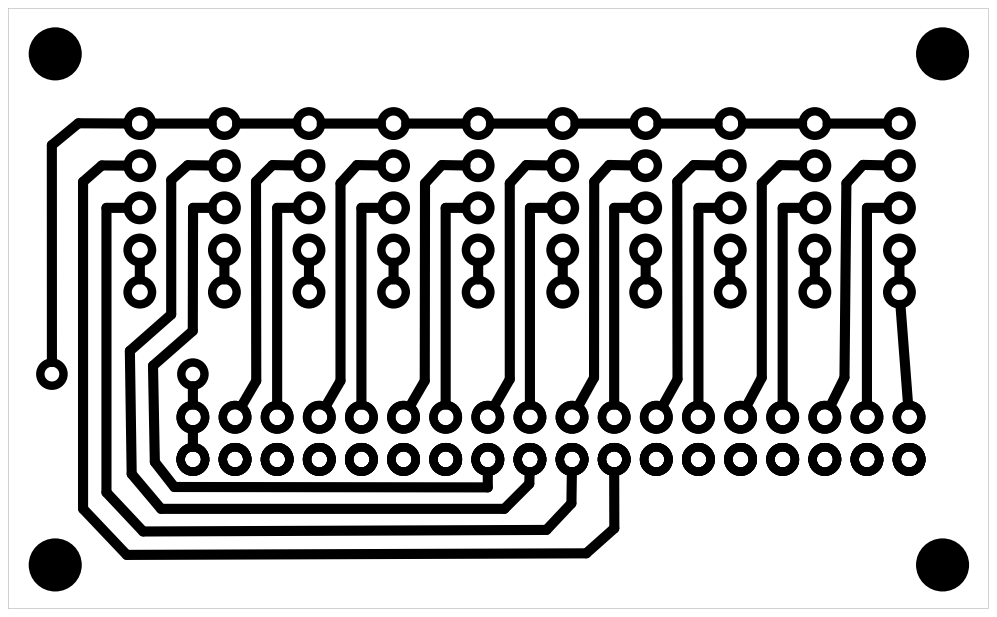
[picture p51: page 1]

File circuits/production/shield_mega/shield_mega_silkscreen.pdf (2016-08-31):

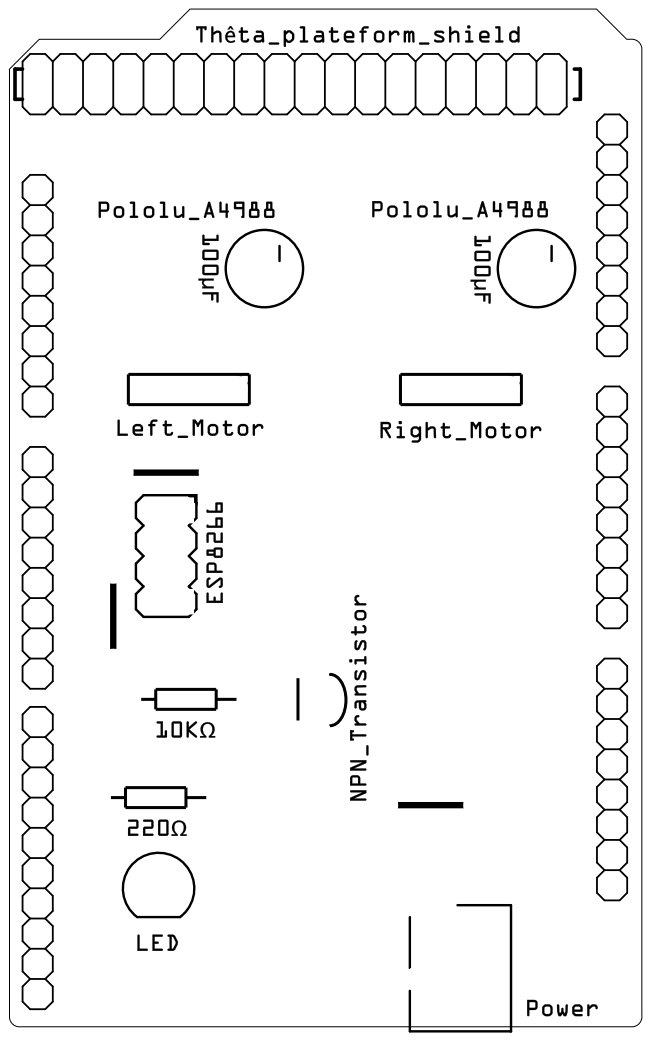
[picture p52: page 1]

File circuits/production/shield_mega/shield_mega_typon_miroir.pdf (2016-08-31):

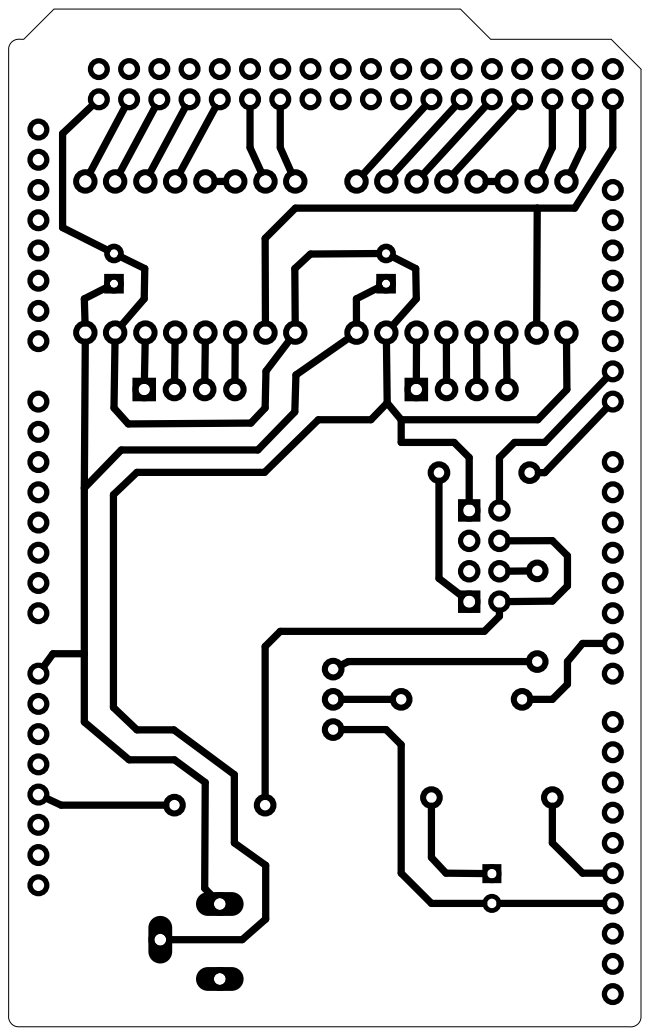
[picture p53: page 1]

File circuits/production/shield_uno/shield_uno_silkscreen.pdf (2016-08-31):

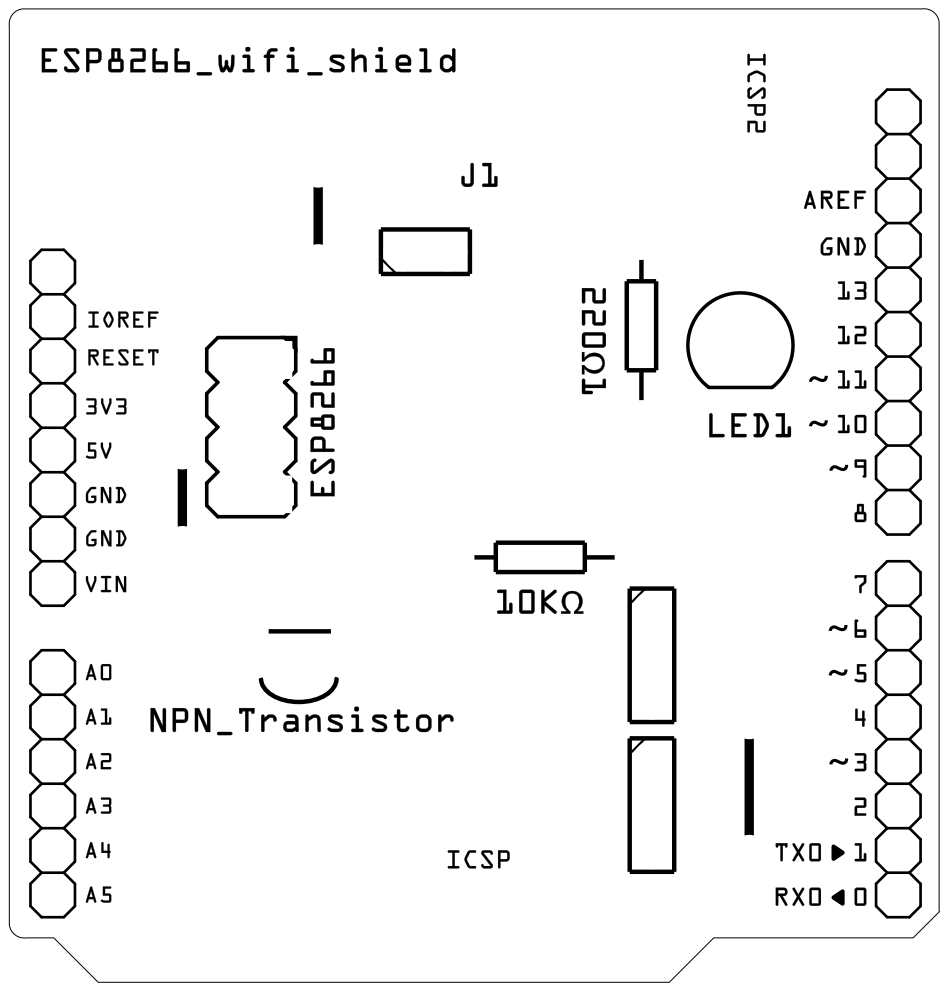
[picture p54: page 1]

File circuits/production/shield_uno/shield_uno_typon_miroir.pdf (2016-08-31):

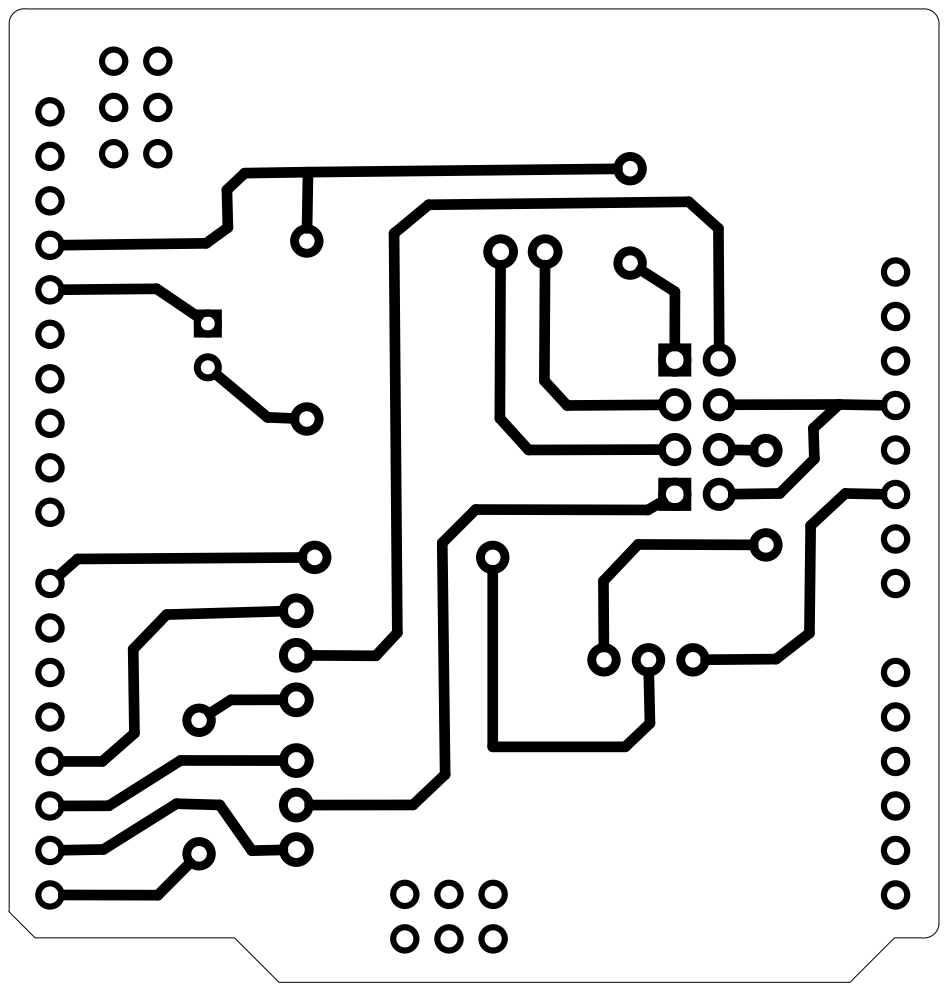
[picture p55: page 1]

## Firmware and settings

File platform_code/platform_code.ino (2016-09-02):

// Copyright (C) 2012, 2013 APO-33
// Author : Matisse V (http://github.com/matissev)
// This file is part of the Thêta Fantômes project.
//
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
// You should have received a copy of the GNU General Public License
//
//
//				                  `/shmNMMMMNmho:`                 
//				                :hMms/-.`  `.-+yNNy.               
//				              `hMh-              /mMo              
//				             `mMo                 `yMy             
//				             dMo                    hMs            
//				            oMh   `oo`    `oo`      `mM/           
//				           -MN.   mMMm    mMMm       -MN.          
//				          -NM:    mMMm    mMMm        +Md.         
//				      .+ymMd-     `++`    `++`         /mMmho:`    
//				    /dMdo:`                              `-+yNNy.  
//				  .dMh-                                       /NM/ 
//				 `mM/                                          .NM:
//				 yMs                                            +Mh
//				 MM+-`                                          .MN
//				 shdmMmy-                                     ..-MM
//				     `/dMs                                /hNMNmmmd
//				       `mM:                              yMh:`     
//				        sMs                             /Md        
//				        /Md                            `mM:        
//				         hMds/-                       :dMo         
//				          -+shNMd+`               :shNNy-          
//				               .sMm-            .dMh+-             
//				                 -NN:          /NN:                
//				                  .dMh/-`  `-+dMd.                 
//				                    -sdNMMMMmho-      
//


// ------------------------------------- INCLUDES -------------------------------------

#include <Tone.h>
#include <NewPing.h>
// Here is a stackoverflow that will help you to resolve the timer compilation error (vector_13), if needed.
// http://stackoverflow.com/questions/17208703/arduino-timer-seems-to-be-crashing
// In NewPing.cpp, also consider replacing :
// TIMER2_COMPA_vect (l.284)
// with
// TIMER3_COMPA_vect

#include "_init.h" // This file contain the constants, like the SSID, the pinout, etc..
#include "wifi.h"
#include "osc.h"
#include "motors.h"
#include "motion.h"


// ------------------------------------- CLASS -------------------------------------


// Communication
Osc_C osc_;
Wifi_C wifi_;


// Motors
Motors_C motors_;
Motion_C motion_;


// ------------------------------------- SETUP -------------------------------------

void setup() {
	Serial.begin(115200); // Serial debug via USB

	Serial.println("****************************************************************");
	Serial.println("************************ Starting setup ************************");
	Serial.println("****************************************************************\n");

	motors_.init(); // Setting up the motors pins
	wifi_.init(); // Connecting to the wifi network

	Serial.println("****************************************************************");
	Serial.println("*************************** Setup OK ***************************"); // Everything's up and running
	Serial.println("****************************************************************\n");
}


// ------------------------------------- LOOP --------------------------------------

void loop() {
	// Update the motion values with the incoming message, line it
	// motion.cpp - osc.cpp
	motion_.update(osc_);

	// Move according to the motion calculated and save it
	// motors.cpp - motion.cpp
	motors_.move(motion_);
}

void serialEvent3() {
	// Grab and parse the OSC message from the Serial
	// wifi.cpp - osc.cpp
	wifi_.receive(osc_);
}

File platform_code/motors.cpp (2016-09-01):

#include "motors.h"

Motors_C::Motors_C() :
	RIGHT_MOTOR {
		RIGHT_MOTOR_ENABLE_PIN,
		RIGHT_MOTOR_DIRECTION_PIN,
		RIGHT_MOTOR_STEP_PIN,
		RIGHT_MOTOR_MS1_PIN,
		RIGHT_MOTOR_MS2_PIN,
		RIGHT_MOTOR_MS3_PIN
	},
	LEFT_MOTOR {
		LEFT_MOTOR_ENABLE_PIN,
		LEFT_MOTOR_DIRECTION_PIN,
		LEFT_MOTOR_STEP_PIN,
		LEFT_MOTOR_MS1_PIN,
		LEFT_MOTOR_MS2_PIN,
		LEFT_MOTOR_MS3_PIN
	},
	areEnabled(true)
{}


void Motors_C::init() {
	// Set motors pins and their values
	pinMode(this->LEFT_MOTOR.ENABLE_PIN, OUTPUT);
	pinMode(this->LEFT_MOTOR.DIRECTION_PIN, OUTPUT);
	pinMode(this->LEFT_MOTOR.STEP_PIN, OUTPUT);
	pinMode(this->LEFT_MOTOR.MS1_PIN, OUTPUT);
	pinMode(this->LEFT_MOTOR.MS2_PIN, OUTPUT);
	pinMode(this->LEFT_MOTOR.MS3_PIN, OUTPUT);

	pinMode(this->RIGHT_MOTOR.ENABLE_PIN, OUTPUT);
	pinMode(this->RIGHT_MOTOR.DIRECTION_PIN, OUTPUT);
	pinMode(this->RIGHT_MOTOR.STEP_PIN, OUTPUT);
	pinMode(this->RIGHT_MOTOR.MS1_PIN, OUTPUT);
	pinMode(this->RIGHT_MOTOR.MS2_PIN, OUTPUT);
	pinMode(this->RIGHT_MOTOR.MS3_PIN, OUTPUT);

	digitalWrite(this->LEFT_MOTOR.ENABLE_PIN, LOW);
	digitalWrite(this->LEFT_MOTOR.DIRECTION_PIN, FORWARDS);
	digitalWrite(this->LEFT_MOTOR.STEP_PIN, LOW);
	digitalWrite(this->LEFT_MOTOR.MS1_PIN, HIGH);
	digitalWrite(this->LEFT_MOTOR.MS2_PIN, HIGH);
	digitalWrite(this->LEFT_MOTOR.MS3_PIN, HIGH);

	digitalWrite(this->RIGHT_MOTOR.ENABLE_PIN, LOW);
	digitalWrite(this->RIGHT_MOTOR.DIRECTION_PIN, FORWARDS);
	digitalWrite(this->RIGHT_MOTOR.STEP_PIN, LOW);
	digitalWrite(this->RIGHT_MOTOR.MS1_PIN, HIGH);
	digitalWrite(this->RIGHT_MOTOR.MS2_PIN, HIGH);
	digitalWrite(this->RIGHT_MOTOR.MS3_PIN, HIGH);

	// Start the tones on the step pin
	this->LEFT_MOTOR.rate.begin(this->LEFT_MOTOR.STEP_PIN);
	this->RIGHT_MOTOR.rate.begin(this->RIGHT_MOTOR.STEP_PIN);
}


void Motors_C::move(Motion_C& motion_) {
	// Change the motors' action only if the calculated motions have changed
	if (motion_.hasChanged()) {
		this->updateDirection(motion_);
		this->updateSpeed(motion_);

		// Backup the values for the next round
		motion_.saveValues();
	}
}


void Motors_C::updateDirection(Motion_C motion_) { // A little bit tricky, have fun.
	int angle = motion_.getAngle();
	int speed = motion_.getSpeed();

	if (angle >= -90 && angle <= 90 && speed > 0) {
		// When you are going FORWARDS and turning a LITTLE, keep the motors FORWARDS
		digitalWrite(this->RIGHT_MOTOR.DIRECTION_PIN, FORWARDS);
		digitalWrite(this->LEFT_MOTOR.DIRECTION_PIN, FORWARDS);
	} else 	if (angle >= -90 && angle <= 90 && speed < 0) {
		// When you are going BACKWARDS and you are not turing or you are turning a LITTLE, keep the motors FORWARDS
		digitalWrite(this->RIGHT_MOTOR.DIRECTION_PIN, BACKWARDS);
		digitalWrite(this->LEFT_MOTOR.DIRECTION_PIN, BACKWARDS);
	} else if ((angle < -90 && speed > 0) || (angle > 90 && speed < 0)) {
		// When you are going FORWARDS and you are turning a LOT ON THE LEFT, send the left motor BACKWARDS and the right one FORWARDS
		// OR when you are going BACKWARDS and you are turning a LOT ON THE RIGHT, send the left motor BACKWARDS and the right one FORWARDS
		digitalWrite(this->RIGHT_MOTOR.DIRECTION_PIN, FORWARDS);
		digitalWrite(this->LEFT_MOTOR.DIRECTION_PIN, BACKWARDS);
	} else if ((angle > 90 && speed > 0) || (angle < -90 && speed < 0)) {
		// When you are going FORWARDS and you are turning a LOT ON THE RIGHT, send the RIGHT motor FORWARDS and the right one BACKWARDS
		// OR when you are going BACKWARDS and you are turning a LOT ON THE LEFT, send the LEFT motor FORWARDS and the right one BACKWARDS
		digitalWrite(this->RIGHT_MOTOR.DIRECTION_PIN, BACKWARDS);
		digitalWrite(this->LEFT_MOTOR.DIRECTION_PIN, FORWARDS);
	}
}


void Motors_C::updateSpeed(Motion_C motion_) {
	int angle = motion_.getAngle();
	int speed = motion_.getSpeed();

	int absAngle = abs(abs(angle) - 90);


	// Re-activate the motors when the speed is kicking
	if (speed != 0 && this->areEnabled == false) {
		this->areEnabled = true;
		digitalWrite(this->RIGHT_MOTOR.ENABLE_PIN, LOW);
		digitalWrite(this->LEFT_MOTOR.ENABLE_PIN, LOW);
	}


	if (angle == 0) {
		// set both motors' speed equaly and go straight when there's no angle value
		this->RIGHT_MOTOR.rate.play(abs(speed));
		this->LEFT_MOTOR.rate.play(abs(speed));
	} else if (angle > 0) {
		// else if the angle is positive, speed down the right motor to turn right
		this->RIGHT_MOTOR.rate.play(abs(speed) * map(absAngle, 0, 90, 0, 100) / 100); // Good luck with this one...
		this->LEFT_MOTOR.rate.play(abs(speed));
	} else if (angle < 0) {
		// else if the angle is negative, speed down the left motor to turn left
		this->RIGHT_MOTOR.rate.play(abs(speed));
		this->LEFT_MOTOR.rate.play(abs(speed) * map(absAngle, 0, 90, 0, 100) / 100);
	}


	// Stop the motors when the speed is null
	if (speed == 0) {
		this->areEnabled = false;
		this->RIGHT_MOTOR.rate.stop();
		this->LEFT_MOTOR.rate.stop();
		digitalWrite(this->RIGHT_MOTOR.ENABLE_PIN, HIGH);
		digitalWrite(this->LEFT_MOTOR.ENABLE_PIN, HIGH);
	}
}

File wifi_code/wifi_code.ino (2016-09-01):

// Copyright (C) 2012, 2013 APO-33
// Author : Matisse V (http://github.com/matissev)
// This file is part of the Thêta Fantômes project.
//
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
// You should have received a copy of the GNU General Public License


#include <ESP8266WiFi.h>
#include <WiFiUdp.h>
#include <esp8266-OSCMessage.h>

// This is necessary in order to change the HOSTNAME
extern "C" {
	#include "user_interface.h"
}

// The code is supporting softwareSerial, which is slower but allows more debuging verbose (than the hardware serial)
#define USE_SOFTWARE_SERIAL false

#if USE_SOFTWARE_SERIAL == true
	#define BAUDRATE 9600
#elif USE_SOFTWARE_SERIAL == false
	#define BAUDRATE 115200
#endif

// Documentation of the OSC library can be found here : https://github.com/CNMAT/OSC
// And the rest of the API is available here : http://cnmat.berkeley.edu/library/oscuino/
// Here is the same library adapted for the esp8266 : https://github.com/sandeepmistry/esp8266-OSC

String SSID;
String PASSWORD;
String HOSTNAME;
int SERVER_PORT;
byte mac[6];

// A UDP instance to let us send and receive packets over UDP
WiFiUDP Udp;

OSCErrorCode error;


void setup() {
	// Serial connection to the arduino
	Serial.begin(BAUDRATE);

	// Give time to the arduino
	delay(200);

	// Let's go
	Serial.println();
	Serial.println("Wifi chip ready");
	Serial.println();

	// Waiting for the SSID
	Serial.println("SSID?");
	SSID = getSerialMessage();

	// Waiting for the PASSWORD
	Serial.println("PASSWORD?");
	PASSWORD = getSerialMessage();

	// Waiting for the SERVER_PORT
	Serial.println("SERVER_PORT?");
	SERVER_PORT = getSerialMessage().toInt();

	// Waiting for the HOSTNAME
	Serial.println("HOSTNAME?");
	HOSTNAME = getSerialMessage();

	// Converting everything from Strings to char arrays
	char ssid[SSID.length() + 1];
	SSID.toCharArray(ssid, SSID.length() + 1);

	char pass[PASSWORD.length() + 1];
	PASSWORD.toCharArray(pass, PASSWORD.length() + 1);

	char hostname[HOSTNAME.length() + 1];
	HOSTNAME.toCharArray(hostname, HOSTNAME.length() + 1);

	// Set up the hostname and the wifi mode
	wifi_station_set_hostname(hostname);
	WiFi.mode(WIFI_STA);

	// Some verbose
	Serial.println();
	Serial.print("*** Connecting to ");
	Serial.print(ssid);
	Serial.println(" ***");
	Serial.println();
	Serial.println();

	// Connecting to wifi network
	WiFi.begin(ssid, pass);
	Serial.println("WiFi connected");

	// Print out the MAC address to the arduino
	WiFi.macAddress(mac);
	Serial.print("MAC : ");
	Serial.print(mac[0],HEX);
	Serial.print(":");
	Serial.print(mac[1],HEX);
	Serial.print(":");
	Serial.print(mac[2],HEX);
	Serial.print(":");
	Serial.print(mac[3],HEX);
	Serial.print(":");
	Serial.print(mac[4],HEX);
	Serial.print(":");
	Serial.println(mac[5],HEX);

	// Print out the IP address to the arduino (does not work for now)
	Serial.print("IP address : ");
	Serial.println(WiFi.localIP());

	// Start the UDP server and print out the port to the arduino
	Serial.println();
	Serial.println("Starting UDP");
	Udp.begin(SERVER_PORT);
	Serial.print("Local port : ");
	Serial.println(Udp.localPort());
	Serial.println();
	Serial.println("All OK");
	Serial.println();
}


String getSerialMessage() {
	// Wait for the next serial message and return it
	String cache;
	while(1){
		if(Serial.available()) {
			cache = Serial.readStringUntil('\n');
			cache.trim();
			break;
		}
	}
	return cache;
}


void loop() {
	OSCMessage message;
	int value = 0;
	char route[200];

	// Get the size of the incoming packet and its remote IP
	int size = Udp.parsePacket();
	IPAddress remoteIp = Udp.remoteIP(); // IP of the sender

	// If there is a packet
	if (size > 0) {
		// Get every byte of the message from this packet
		while (size--) {
			message.fill(Udp.read());
		}

		if (!message.hasError()) {
			// If the message is sane, unpack it and send it to the arduino
			message.getAddress(route);
			value = message.getInt(0);

			Serial.print("OSC ");
			Serial.print(remoteIp);
			Serial.print(" ");
			Serial.print(route);
			Serial.print(" ");
			Serial.println(value);
		} else {
			// If the message is not sane, print out the error
			error = message.getError();
			Serial.print("error: ");
			Serial.println(error);
		}
	}
}

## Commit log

2016-08-31 Added documentations of the Delta Micro 3D printer
    [calibre.STL]
2016-09-01 Plateform code comments
2016-09-01 The lasers are clean and now supports blink
    [laser_scheme.fzz, platform_scheme.fzz, sensors.fzz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]
2016-09-01 Goodbye bugs, on plateforms
    [platform_code.ino]
2016-09-02 3d parts update
    [arduino_mount.stl, essieu.stl, plaques.FCStd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]

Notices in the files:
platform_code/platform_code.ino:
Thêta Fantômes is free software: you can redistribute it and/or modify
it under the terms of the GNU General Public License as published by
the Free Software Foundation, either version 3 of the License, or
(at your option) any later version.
